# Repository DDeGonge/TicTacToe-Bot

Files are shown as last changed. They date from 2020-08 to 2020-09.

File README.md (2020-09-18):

# TicTacToe-Bot
Its a robot that plays tic tac toe.....

Build at your own risk, documentation is limited and the BOM below is NOT verified.

## BOM
* ~300g filament
* 4x 625 bearings
* 3x low profile gt2 20t 6mm drive pulleys
* 200mm gt2 closed loop belt
* 240mm gt2 closed loop belt
* 11x M3x6 SHCS (*BHCS probably better*) bolt. 4x more for the electronics box lid.
* 5x M3x16 SHCS bolts. Maybe get some M3x18 too just in case :D
* 1x M5x16 SHCS bolt
* 1x M5x40 SHCS bolt
* 2x M5 Nut
* 6x M3 Nut
* A few M3 and M5 washers
* some paper clips to connect servo to pen sleeve
* Uniball 60151 pen, or any other that are a similar size to fit in the sleeve.
* Some M2 bolt and nuts for raspberry pi camera mounting

* 2x nema 17 steppers, <=40mm length
* 1x mg90 servo
* Raspberry pi zero w
* Raspberry pi camera V1.X
* Adafruit Feather M4 or similar
* Stepper drivers, mine go one a custom pcb (files in repo) but you can solder your own or buy an OTS one
* MAX98357 I2S Audio Amplifier Module
* 8 ohm speaker

If you find any errors, please open an issue ticket!

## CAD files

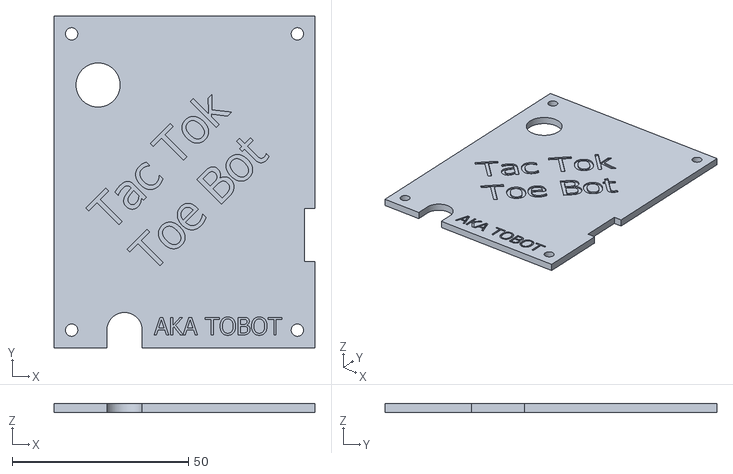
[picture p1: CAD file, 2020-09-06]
cad/Electronics Lid.stl
74.0 x 94.0 x 2.50

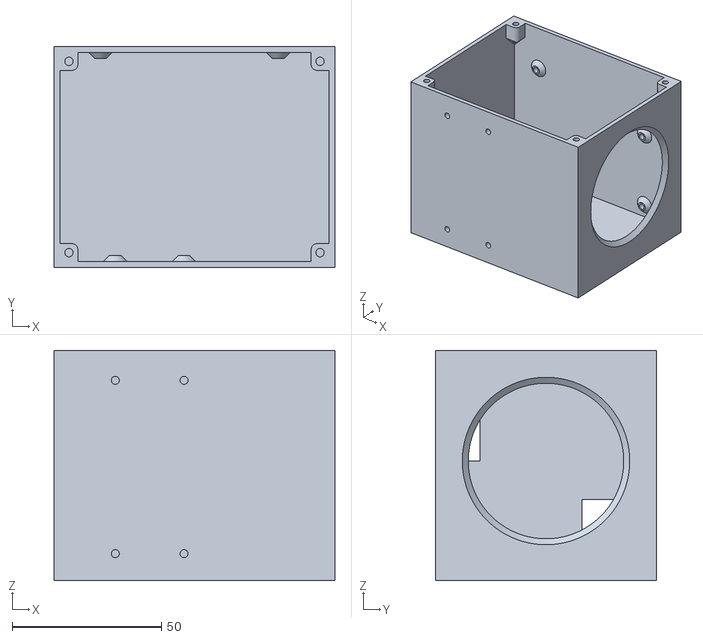
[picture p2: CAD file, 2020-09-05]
cad/Electronics Box.stl
94.0 x 74.0 x 77.0

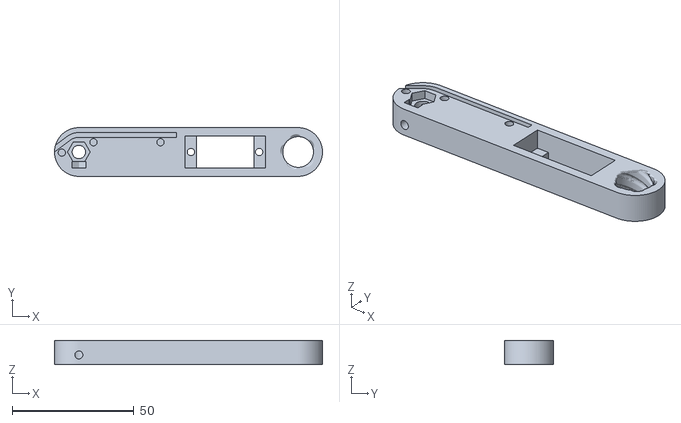
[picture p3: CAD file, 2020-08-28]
cad/Scara2.stl
110.0 x 20.0 x 10.0

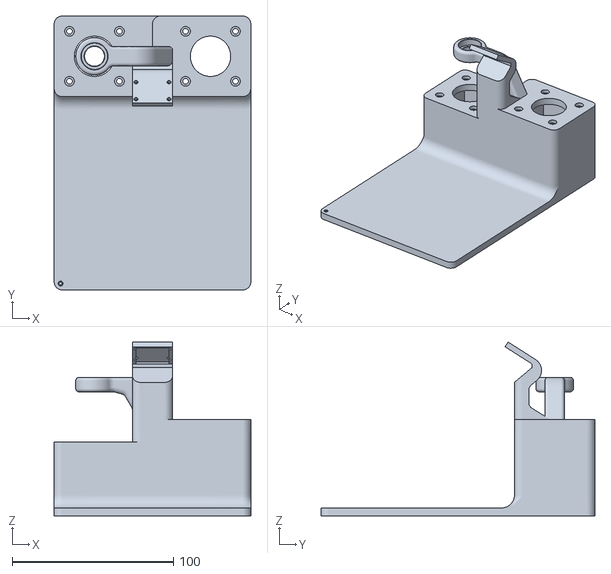
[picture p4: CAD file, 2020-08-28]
cad/Base.stl
122.0 x 170.0 x 107.9

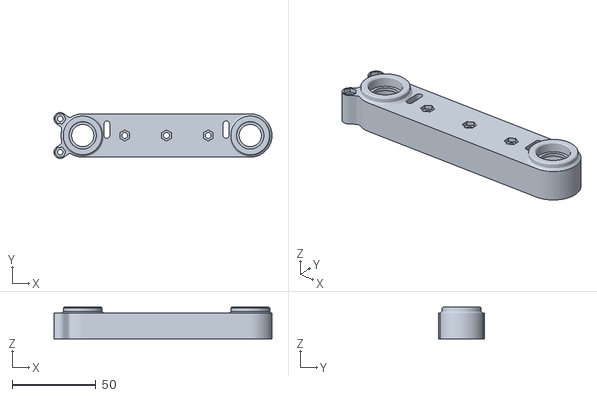
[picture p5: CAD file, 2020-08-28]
cad/Scara1.stl
130.5 x 27.5 x 19.0

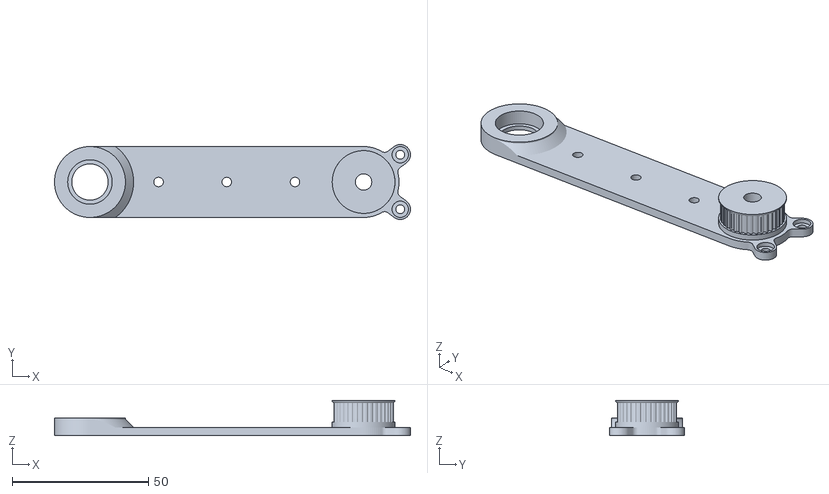
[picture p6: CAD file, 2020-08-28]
cad/Scara1_top.stl
130.5 x 27.5 x 13.0

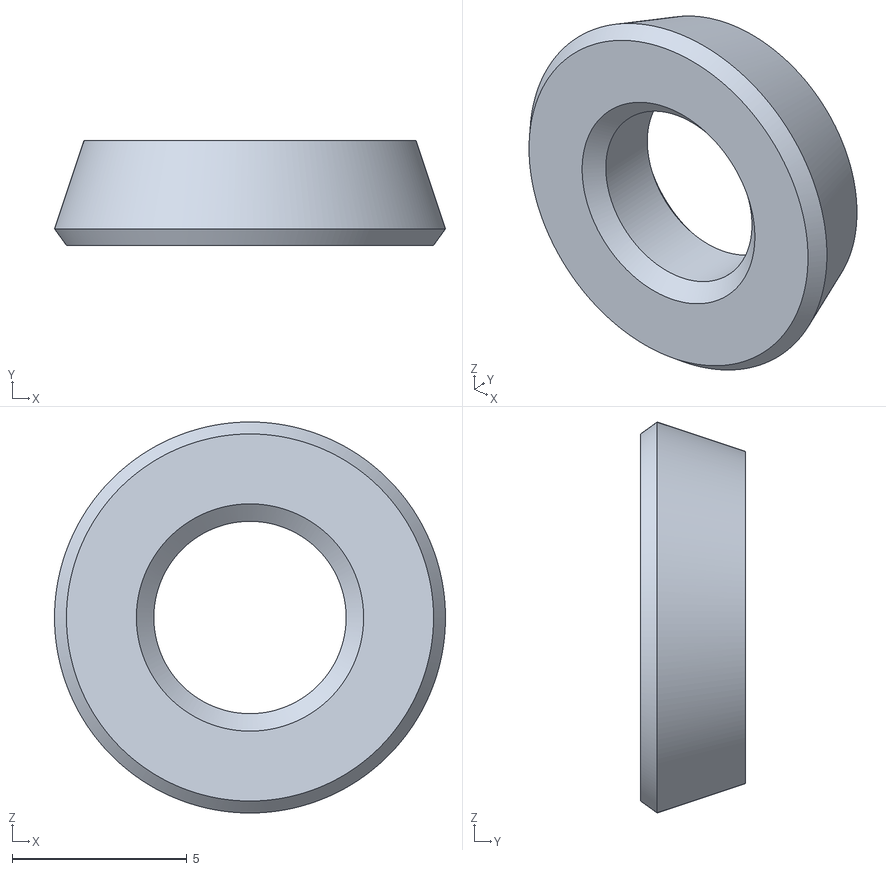
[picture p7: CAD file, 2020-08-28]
cad/PulleySpacer.stl
11.2 x 3.00 x 11.2

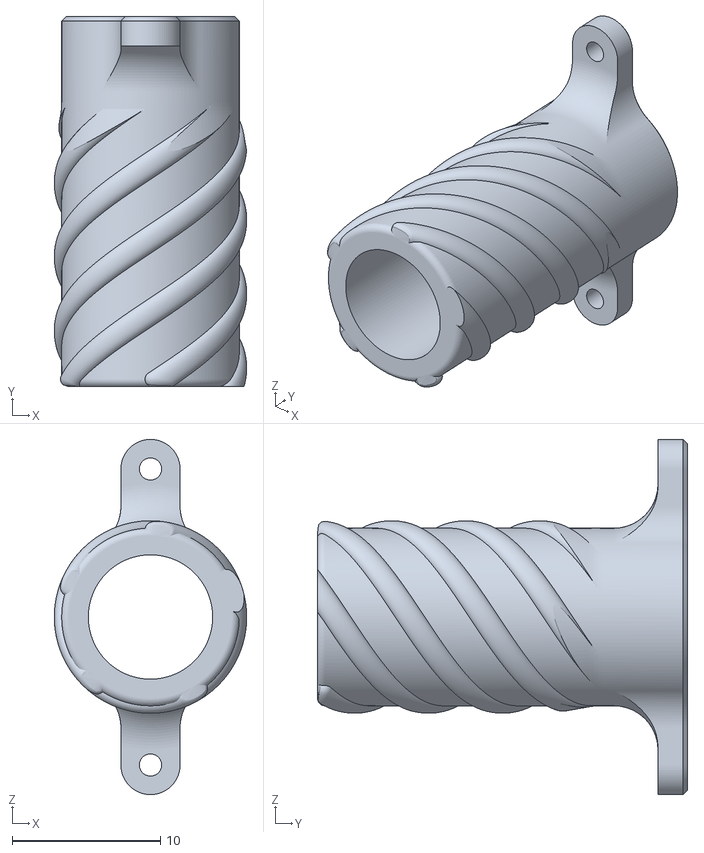
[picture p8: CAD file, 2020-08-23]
cad/Pen Sleeve.stl
13.0 x 25.0 x 24.0

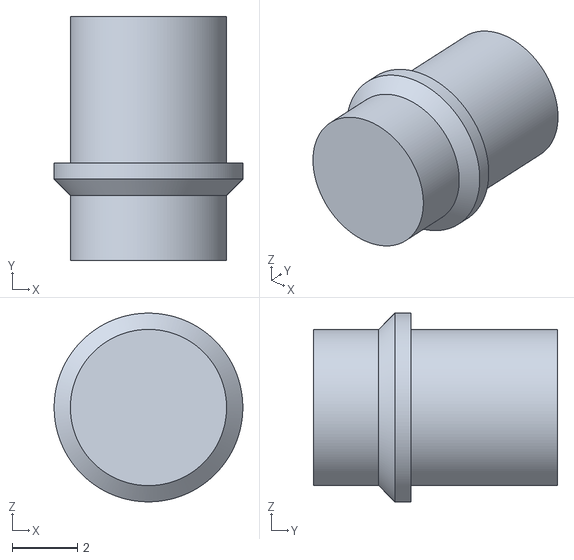
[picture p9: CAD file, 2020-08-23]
cad/Stepper Shaft Extension.stl
5.80 x 7.50 x 5.80

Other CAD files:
cad/625 Bearing.ipt
cad/Base.ipt
cad/Electronics Box.ipt
cad/Electronics Lid.ipt
cad/GT2 20T Drive Pulley.ipt
cad/GT2 Idler Pulley.ipt
cad/MG90servo_body.ipt
cad/Main Assembly.iam
cad/Nema 17.ipt
cad/OldVersions/Base.0059.ipt
cad/OldVersions/Electronics Box.0004.ipt
cad/OldVersions/Main Assembly.0053.iam
cad/OldVersions/Pen Sleeve.0014.ipt
cad/OldVersions/PulleySpacer.0001.ipt
cad/OldVersions/Scara1.0039.ipt
cad/OldVersions/Scara1_top.0033.ipt
cad/OldVersions/Scara2.0021.ipt
cad/OldVersions/Stepper Shaft Extension.0001.ipt
cad/OldVersions/pen.0001.ipt
cad/OldVersions/scara math.0005.ipt
cad/Pen Sleeve.ipt
cad/PulleySpacer.ipt
cad/Scara1.ipt
cad/Scara1_top.ipt
cad/Scara2.ipt
cad/Stepper Shaft Extension.ipt
cad/pen.ipt
cad/scara math.ipt

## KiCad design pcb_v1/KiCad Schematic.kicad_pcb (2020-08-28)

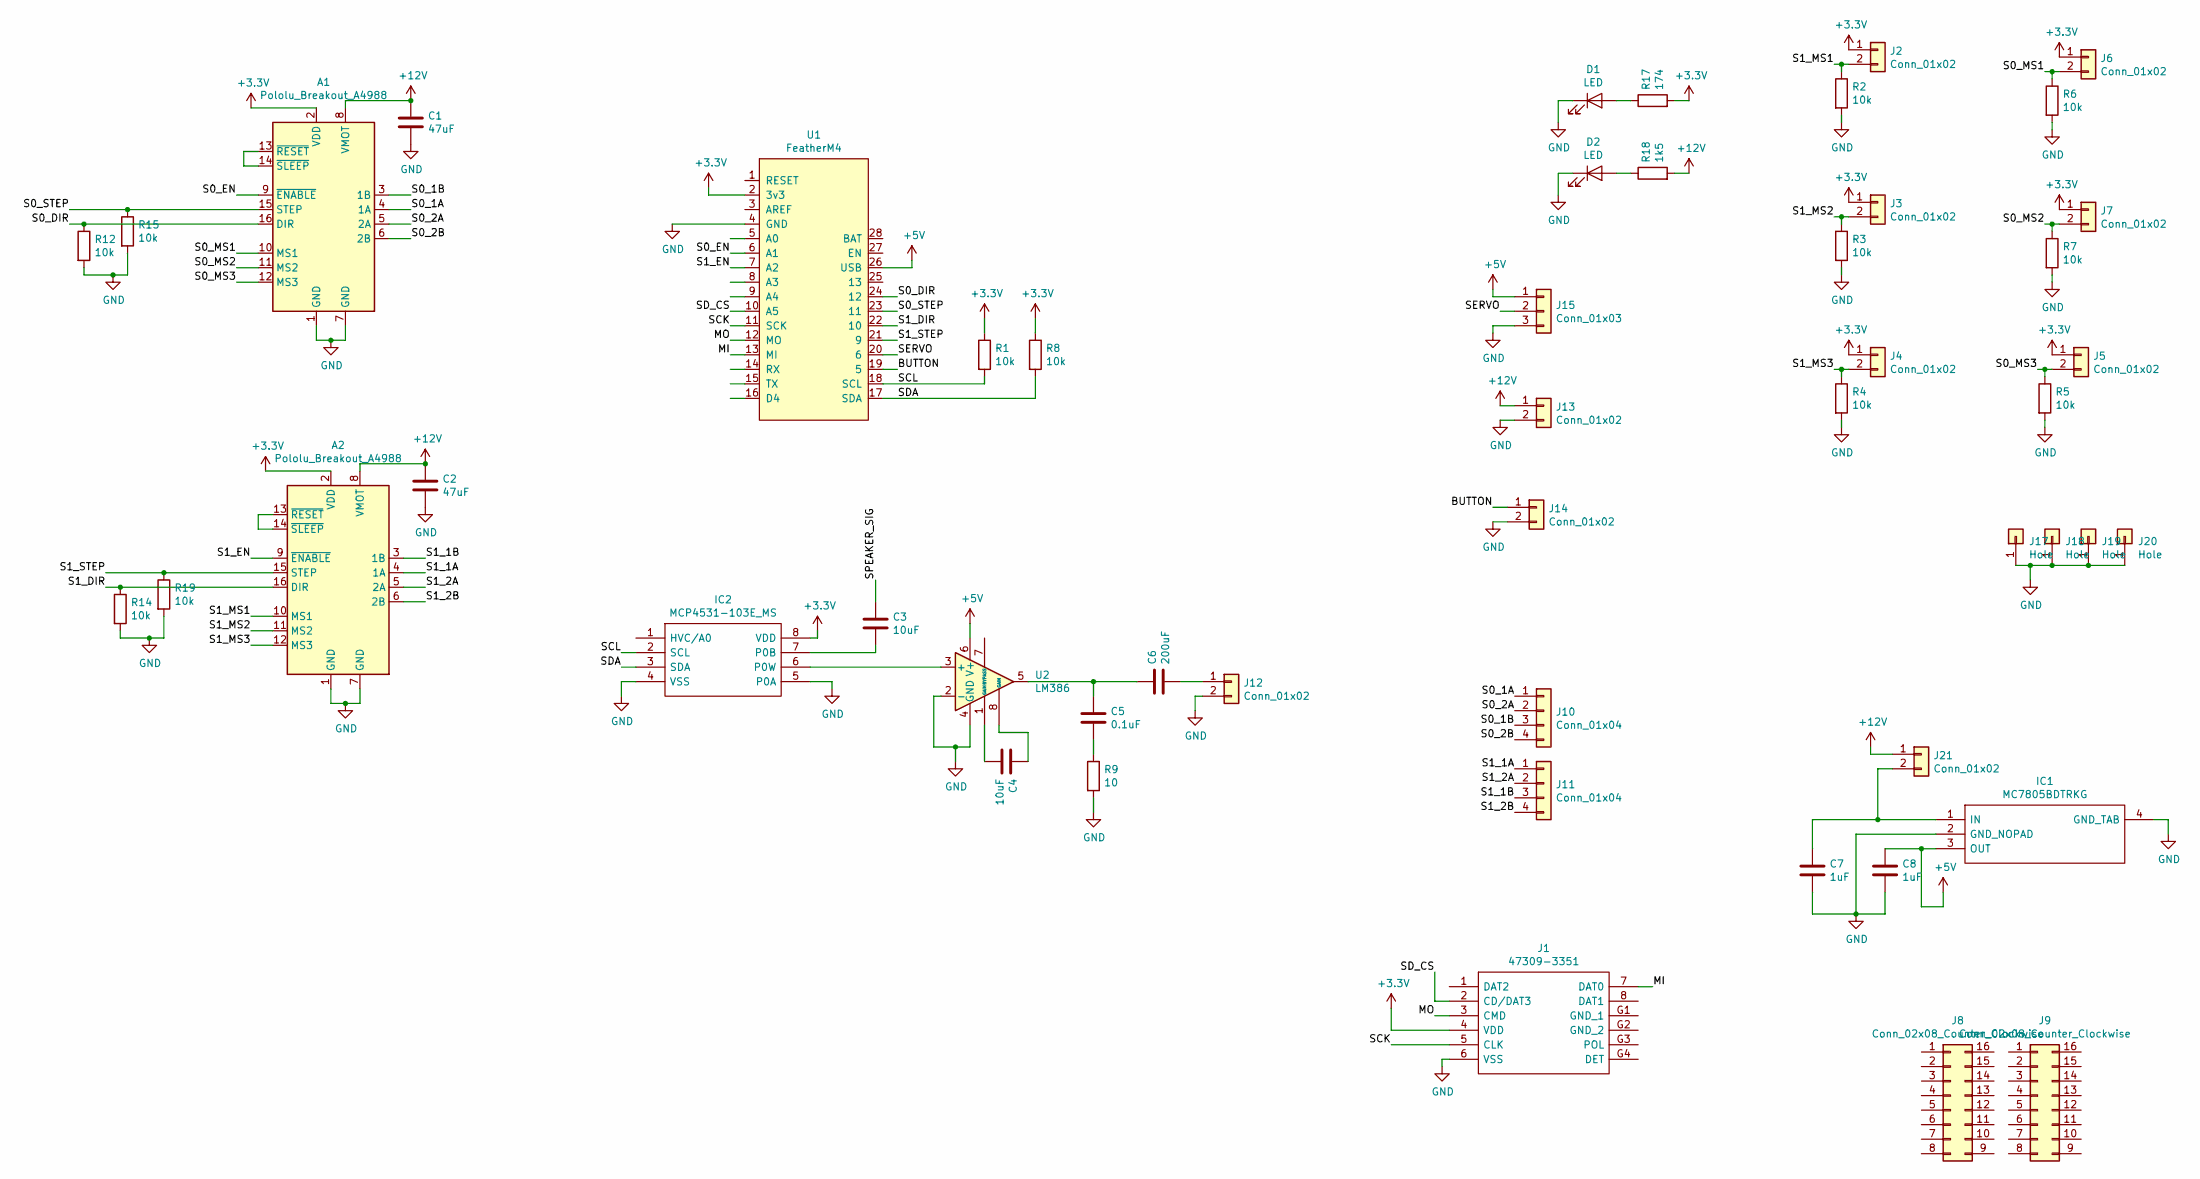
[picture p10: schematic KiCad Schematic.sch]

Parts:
A1, A2: Pololu_Breakout_A4988; Pololu_Breakout-16_15.2x20.3mm
C1, C2: 47uF; CP_Elec_6.3x5.8
C3, C4: 10uF; C_Radial_D5.0mm_H11.0mm_P2.00mm
C5: 0.1uF; C_0402_1005Metric
C6: 200uF; C_Radial_D6.3mm_H7.0mm_P2.50mm
C7, C8: 1uF; C_1206_3216Metric
D1, D2: LED; LED_0603_1608Metric
IC1: MC7805BDTRKG; TO229P990X238-4N; Mouser Part Number 863-MC7805BDTRKG
IC2: MCP4531-103E_MS; SOP65P490X110-8N; Mouser Part Number 579-MCP4531-103E/MS
J1: 47309-3351; 473093351; Mouser Part Number 538-47309-3351
J2, J3, J4, J5, J6, J7, J12, J14, J21: Conn_01x02; PinHeader_1x02_P2.54mm_Vertical
J8, J9: Conn_02x08_Counter_Clockwise; PinHeader_2x08_P2.54mm_Vertical
J10, J11: Conn_01x04; PinSocket_1x04_P2.54mm_Vertical
J13: Conn_01x02; BarrelJack_Wuerth_6941xx301002
J15: Conn_01x03; PinHeader_1x03_P2.54mm_Vertical
J17, J18, J19, J20: Hole; MountingHole_2.7mm_M2.5_DIN965_Pad
R1, R2, R3, R4, R5, R6, R7, R8, R12, R14, R15, R19: 10k; R_0603_1608Metric
R9: 10; R_0603_1608Metric
R17: 174; R_0603_1608Metric
R18: 1k5; R_0603_1608Metric
U1: FeatherM4; FeatherFootprint
U2: LM386; SOIC-8_3.9x4.9mm_P1.27mm

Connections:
+3V3: A1.2 (VDD), A2.2 (VDD), IC2.8 (VDD), J1.4 (VDD), J2.1, J3.1, J4.1, J5.1, J6.1, J7.1, R1.1, R8.1, R17.2, U1.2 (3v3)
+5V: C8.1, IC1.3 (OUT), J15.1, U1.26 (USB), U2.6 (V+)
+12V: A1.8 (VMOT), A2.8 (VMOT), C1.1, C2.1, J13.1, J21.1, R18.2
/BUTTON: J14.1, U1.19 (5)
/MI: J1.7 (DAT0), U1.13 (MI)
/MO: J1.3 (CMD), U1.12 (MO)
/S0_1A: A1.4 (1A), J10.1
/S0_1B: A1.3 (1B), J10.3
/S0_2A: A1.5 (2A), J10.2
/S0_2B: A1.6 (2B), J10.4
/S0_DIR: A1.16 (DIR), R12.1, U1.24 (12)
/S0_EN: A1.9 (~ENABLE), U1.6 (A1)
/S0_MS1: A1.10 (MS1), J6.2, R6.1
/S0_MS2: A1.11 (MS2), J7.2, R7.1
/S0_MS3: A1.12 (MS3), J5.2, R5.1
/S0_STEP: A1.15 (STEP), R15.1, U1.23 (11)
/S1_1A: A2.4 (1A), J11.1
/S1_1B: A2.3 (1B), J11.3
/S1_2A: A2.5 (2A), J11.2
/S1_2B: A2.6 (2B), J11.4
/S1_DIR: A2.16 (DIR), R14.1, U1.22 (10)
/S1_EN: A2.9 (~ENABLE), U1.7 (A2)
/S1_MS1: A2.10 (MS1), J2.2, R2.1
/S1_MS2: A2.11 (MS2), J3.2, R3.1
/S1_MS3: A2.12 (MS3), J4.2, R4.1
/S1_STEP: A2.15 (STEP), R19.1, U1.21 (9)
/SCK: J1.5 (CLK), U1.11 (SCK)
/SCL: IC2.2 (SCL), R1.2, U1.18 (SCL)
/SDA: IC2.3 (SDA), R8.2, U1.17 (SDA)
/SD_CS: J1.2 (CD/DAT3), U1.10 (A5)
/SERVO: J15.2, U1.20 (6)
/SPEAKER_SIG: C3.1
GND: A1.1 (GND), A1.7 (GND), A2.1 (GND), A2.7 (GND), C1.2, C2.2, C7.2, C8.2, D1.1 (K), D2.1 (K), IC1.2 (GND_NOPAD), IC1.4 (GND_TAB), IC2.4 (VSS), IC2.5 (P0A), J1.6 (VSS), J12.2, J13.2, J14.2, J15.3, J17.1, J18.1, J19.1, J20.1, R2.2, R3.2, R4.2, R5.2, R6.2, R7.2, R9.2, R12.2, R14.2, R15.2, R19.2, U1.4 (GND), U2.2 (-), U2.4 (GND)
unnamed: A1.13 (~RESET), A1.14 (~SLEEP)
unnamed: A2.13 (~RESET), A2.14 (~SLEEP)
unnamed: C3.2, IC2.7 (P0B)
unnamed: C4.1, U2.8 (GAIN)
unnamed: C4.2, U2.1 (GAIN)
unnamed: C5.1, C6.1, U2.5
unnamed: C5.2, R9.1
unnamed: C6.2, J12.1
unnamed: C7.1, IC1.1 (IN), J21.2
unnamed: D1.2 (A), R17.1
unnamed: D2.2 (A), R18.1
unnamed: IC2.6 (P0W), U2.3 (+)

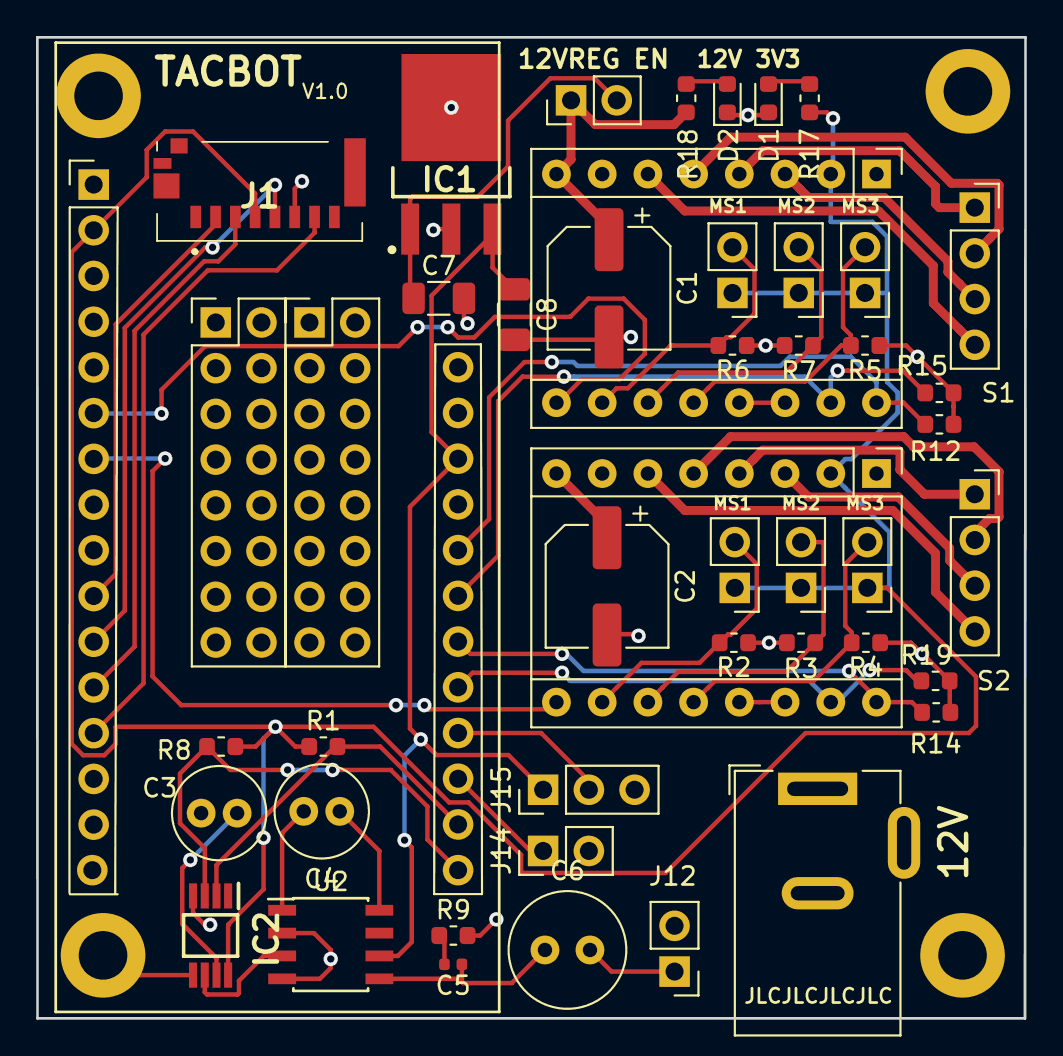
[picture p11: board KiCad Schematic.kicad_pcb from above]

Board: 2 copper layers, 54.9 x 54.5 mm, 51 parts (0 on the bottom side), 44 nets.

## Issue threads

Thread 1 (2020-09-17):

A couple clarifications

kmatch98, 2020-09-17:

kmatch98, 2020-09-17:
First, this is awesome!  End of last year I made a two link robot arm and wanted to make a GCode plotter but I couldn’t stomach to do the math and so I just let it lie dormant. Thanks for doing this!

I have a couple of questions for you:
1.  What does this x and y offset mean?  Maybe a napkin drawing would help?
```
float x0_offset_mm = 25;
 float y0_offset_mm = 135;
```

2.  I see that the homing routine isn’t written, but how do you manage it anyway? Maybe related to above, If my homing position is different would the homing position affect the offsets?

3.  The arc drawing is missing. Do you have a way of generating gcode with only lines?

Thanks a lot for this, and thanks for sharing.

DDeGonge, 2020-09-17:
Sorry I'm pretty terrible at documenting things, I intend to at least improve the readme by the weekend!

1. These are the distances from the 0,0 position to the point of rotation where the first arm connects to the base. Basically where the scara arm starts.

2. I do have a janky "homing" routine function which simply allows you to move the bot so the pen is near zero, it then enables the motor and lets you fine tune the position before accepting. It isn't great but I didn't add any limit switches to the hardware so this was the best I could do haha.

3. I just use Cura and added custom retraction code for my pen. It seems to not use any arcs in the gcode it produces but your results may vary. You could always take a crack at implementing arc control, I'd be happy to merge it into my code if you are successful :D

Closed 2020-09-18.

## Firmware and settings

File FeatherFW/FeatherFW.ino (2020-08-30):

#include "tacbot.h"
#include "funks.h"

#define Serial SERIAL_PORT_USBVIRTUAL

// Speaker stuff
//Adafruit_VS1053_FilePlayer musicPlayer = 
//  Adafruit_VS1053_FilePlayer(VS1053_RESET, VS1053_CS, VS1053_DCS, VS1053_DREQ, CARDCS);

void setup()
{
  // Init serial, sd, musicplayer, and neopixel
  Serial.begin(250000);
  while (!Serial) { delay(1); }
  pixel.begin();
//  if (! musicPlayer.begin()) { // initialise the music player
//     Serial.println(F("Couldn't find VS1053, do you have the right pins defined?"));
//     error_blink(2);
//  }
//  Serial.println(F("VS1053 found"));
//
//  if (!SD.begin(CARDCS)) {
//    Serial.println("SD initialization failed.");
//    error_blink(3);
//  } else {
//    Serial.println("SD initialization successful.");
//  }

  // Configure music player
//  musicPlayer.setVolume(1,1);  // Lower values is louder. I only use right channel
//  musicPlayer.useInterrupt(VS1053_FILEPLAYER_PIN_INT);
}

void loop()
{
  // Initialize some stuff
  setLEDColor(200, 0, 0);
  unsigned long startTime_us = micros();
  unsigned long t_elapsed_us;
  Servo pen_servo;
  pen_servo.attach(servo_pin);
  stepper s0, s1;
  s0.init(s0_step, s0_dir, s0_en, false);
  s1.init(s1_step, s1_dir, s1_en, false);

  scara_bot bot;
  bot.init(s0, s1, pen_servo);

  char serial_data[MAX_MSG_LEN];
  setLEDColor(100, 0, 0);

  // Init vars
  char base_cmd, char_value;
  int32_t base_value, int_value;
  float float_value;

  // Start main response loop
  while (true)
  {
    t_elapsed_us = micros() - startTime_us;
    clear_data(serial_data);
    if (respondToSerial(serial_data)) 
    {
      setLEDColor(100, 50, 0);

      // Parse input into data chunks
      vector<string> args;
      parse_inputs(serial_data, args);
      parse_int(args[0], base_cmd, base_value);

      switch (tolower(base_cmd)) 
      {
        case 'g': {
          switch (base_value) 
          {
            case 0:
            case 1: {
              // LINEAR MOVE
              float xpos, ypos, feedrate;
              gcode_command_floats gcode(args);
              bot.move_motor_linear(gcode.fetch('x'), gcode.fetch('y'), gcode.fetch('f'));
              break;
            }
            case 2: {
              // ARC MOVE CW
              gcode_command_floats gcode(args);
              bot.move_motor_arc(gcode.fetch('x'), gcode.fetch('y'), gcode.fetch('i'), gcode.fetch('j'), gcode.fetch('f'), true);
              break;
            }
            case 3: {
              // ARC MOVE CCW
              gcode_command_floats gcode(args);
              bot.move_motor_arc(gcode.fetch('x'), gcode.fetch('y'), gcode.fetch('i'), gcode.fetch('j'), gcode.fetch('f'), false);
              break;
            }
            case 28: {
              Serial.println("TODO homing");
              break;
            }
            case 90: {
              // Absolute positioning
              bot.set_pos_mode(true);
              break;
            }
            case 91: {
              // Relative positioning
              bot.set_pos_mode(false);
              break;
            }
            case 92: {
              // This is implemented wrong currently but idc deal with it
              gcode_command_floats gcode(args);
              bot.zero(gcode.fetch('x'), gcode.fetch('y'));
              break;
            }
          }
          break;
        }
      case 'm': {
          switch (base_value) 
          {
            case 17: {
              // Enable Steppers
              gcode_command_floats gcode(args);
              bot.enable_motors(gcode.com_exists('x'), gcode.com_exists('y'));
              break;
            }
            case 84: {
              // Disable Steppers
              gcode_command_floats gcode(args);
              bot.disable_motors(gcode.com_exists('x'), gcode.com_exists('y'));
              break;
            }
            case 114: {
              // Get current position
              float xpos, ypos;
              bot.get_pos(xpos, ypos);
              Serial.println("TODO FINISH THIS ONE");
              break;
            }
            case 201: {
              // Set Acceleration Limits
              gcode_command_floats gcode(args);
              bot.set_def_speeds(gcode.fetch('a'), gcode.fetch('v'));
              break;
            }
          }
          break;
        }
      case 'c': {
          switch (base_value) 
          {
            case 0: {
              // configure hardware stuff
              gcode_command_floats gcode(args);
              bot.configure(gcode.fetch('a'), gcode.fetch('b'), gcode.fetch('c'), gcode.fetch('d'), gcode.fetch('e'), gcode.fetch('f'), gcode.fetch('g'), gcode.fetch('h'));
              break;
            }
            case 1: {
              // Lower pen servo
              bot.lower_pen();
              break;
            }
            case 2: {
              // Raise pen servo
              bot.raise_pen();
              break;
            }
            case 3: {
              // Play a tune!
              string str = "/" + args[1] + ".mp3";
              const char* strdata = str.data();
//              musicPlayer.playFullFile(strdata);
              break;
            }
          }
        }
        break;
      }
      Serial.println("ok");
      setLEDColor(0, 100, 0);
    }
  }
}

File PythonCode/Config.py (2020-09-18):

""" DEBUG PARAMS """
DEBUG_MODE = False


""" MECHANICAL PARAMETERS """
s0_step_per_rev = 5760
s1_step_per_rev = 3200

# default_vel_mmps = 800.0
# default_accel_mmps2 = 40000.0
default_vel_mmps = 250.0
default_accel_mmps2 = 10000.0

s0_arm_len_mm = 100.5
s1_arm_len_mm = 90.0

pen_up_pwm = 100
pen_dn_pwm = 70

x_zero_offset = 21
y_zero_offset = 141

board_center_x_mm = 60
board_center_y_mm = 50
box_size_mm = 20


""" OPERATION PARAMETERS """
gcode_folder = 'gcode'
audio_path = 'audio'


""" CAMERA PARAMETERS """
# Cropped region corner points, consider rotation plz
p0 = [145, 115] # TL
p1 = [520, 100] # TR
p2 = [175, 400] # BL
p3 = [470, 385] # BR

IMAGE_RESOLUTION = (648,486)
IMAGE_ROTATION_DEGS = 0

POST_TRANSFORM_RES = [400,400]

TAC_BOX_CENTERS = [
    (67, 67),
    (67, 200),
    (67, 333),
    (200, 67),
    (200, 200),
    (200, 333),
    (333, 67),
    (333, 200),
    (333, 333)
]

TAC_BOX_X = 90
TAC_BOX_Y = 90


""" OPENCV PARAMETERS """
MOTION_MIN_CHANGE = 1.0


""" SPEAKER PARAMETERS """
freq = 44100    # audio CD quality
bitsize = -16   # unsigned 16 bit
channels = 2    # 1 is mono, 2 is stereo
buffer = 2048   # number of samples (experiment to get right sound)
volume = 0.95


""" FEATHER COMM PARAMETERS """
# Chars used for setting parameters on feather. All vars here must be int
Feather_Parameter_Chars = {
    'a': s0_arm_len_mm,
    'b': s1_arm_len_mm,
    'c': s0_step_per_rev,
    'd': s1_step_per_rev,
    'e': x_zero_offset,
    'f': y_zero_offset,
    'g': pen_up_pwm,
    'h': pen_dn_pwm
}

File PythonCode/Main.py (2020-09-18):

__version__ = '0.1.0'

import time
import Config as cfg
import random
from SerialDevice import *
from ScaraDriver import *
from CameraDriver import *
from SpeakerDriver import *
from OtherStuff import *
from Gameplay import *


def main():
    try:
        serdev = SerialDevice()
        scarabot = Scara(serdev)
        cam = Camera()
        spkr = Speaker()

        scarabot.user_zero()
        scarabot.park()
        cam.start_camera()

        while True:
            inpt = input('Press enter to start game...')

            # Future improvements can happen here
            bot_first = True  # random.choice([True, False])
            game_function = 'standard'  # random.choice(GAMETYPES)

            if inpt == 'c':
                spkr.set_cat_mode()
            else:
                spkr.set_human_mode()

            # Start game
            if game_function == 'standard':
                standard_game(scarabot, cam, spkr, bot_first = bot_first)
            elif game_function == 'meme':
                meme_game(scarabot, cam, spkr, bot_first = bot_first)

            scarabot.park()
                
    except Exception as e:
        raise e


if __name__=='__main__':
    # main()

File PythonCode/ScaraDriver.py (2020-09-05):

__version__ = '0.1.0'

import Config as cfg
import os
import time
import math

class Scara(object):
    def __init__(self, serial_device):
        self.serial_device = serial_device
        self.x_error = 0.
        self.y_error = 0.
        self.configure()
        self.update_defaults()
        self.is_parked = False

    """ Motion stuff """

    def configure(self):
        command_string = 'C0'
        for k, v in cfg.Feather_Parameter_Chars.items():
            command_string += ' {}{}'.format(k, v)
        self.serial_device.command(command_string)

    def home(self):
        print('TODO implement this plz')

    def zero(self):
        self.serial_device.command('G92 X0 Y0')

    def enable(self):
        self.serial_device.command('M17')

    def disable(self):
        self.serial_device.command('M84')

    def user_zero(self):
        # Too lazy to implement limit switches so now I have to do this..
        self.disable()
        self.lower_pen()
        _ = input('Press enter when near zero...')
        self.enable()
        while True:
            com = input('Enter commands to move closer to zero in format "x,y", units are mm. Or press enter to continue: ')
            if com == '':
                break
            else:
                com = com.split(',')
                if len(com) == 2:
                    self.zero()
                    self.absolute_move(float(com[0]), float(com[1]))

        self.zero()
        self.raise_pen()

    def park(self):
        if self.is_parked is False:
            self.serial_device.command('G1 X-30 Y90')
            self.serial_device.command('G1 Y130')
        self.is_parked = True

    def unpark(self):
        if self.is_parked is True:
            self.serial_device.command('G1 X-30 Y90')
            self.serial_device.command('G1 X0 Y0')
        self.is_parked = False

    def raise_pen(self):
        self.serial_device.command('C2')

    def lower_pen(self):
        self.serial_device.command('C1')

    def update_defaults(self, vel = None, acc = None):
        if acc == None:
            acc = cfg.default_accel_mmps2
        if vel == None:
            vel = cfg.default_vel_mmps
        self.serial_device.command('M201 a{} v{}'.format(acc, vel))

    def absolute_move(self, xtar_mm, ytar_mm, velocity_mmps=None):
        # Calculate move
        command = 'G0 X{} Y{}'.format(xtar_mm, ytar_mm)
        if velocity_mmps is not None:
            command += ' F{}'.format(velocity_mmps * 60)
        self.serial_device.command(command)

    def relative_move(self, xtar_mm, ytar_mm, velocity_mmps=None):
        return self.absolute_move(xpos_mm + xtar_mm, ypos_mm + ytar_mm, velocity_mmps)

    def draw_move(self, move):
        x_center = cfg.board_center_x_mm + (move.x - 1) * cfg.box_size_mm
        y_center = cfg.board_center_y_mm + (1 - move.y) * cfg.box_size_mm
        self.absolute_move(x_center, y_center)
        self.send_gcode('draw_x.g')

    def draw_board(self):
        self.send_gcode('board.g')

    def draw_win_line(self, game):
        if game is None:
            return

        p_start, p_end = game.get_winner_coords()
        p_start_x = cfg.board_center_x_mm + (p_start[0] - 1) * cfg.box_size_mm
        p_start_y = cfg.board_center_y_mm + (1 - p_start[1]) * cfg.box_size_mm
        p_end_x = cfg.board_center_x_mm + (p_end[0] - 1) * cfg.box_size_mm
        p_end_y = cfg.board_center_y_mm + (1 - p_end[1]) * cfg.box_size_mm
        self.absolute_move(p_start_x, p_start_y)
        self.lower_pen()
        self.absolute_move(p_end_x, p_end_y, 100)
        self.raise_pen()

    def send_gcode(self, filename):
        with open(os.path.join(cfg.gcode_folder, filename)) as f:
            while(True):
                line = f.readline().strip('\n')
                if not line:
                    break
                
                if line[0] == ';':
                    # Comments start with semicolon
                    continue

                self.serial_device.command(line)

    @property
    def is_homed(self):
        return True

    @property
    def xpos_mm(self):
        return

    @property
    def ypos_mm(self):
        return

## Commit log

2020-08-23 update cam driver and test script
2020-08-23 bugfixes, finish initial game loop, stuff
    [CameraDriver.py, Config.py, Gameplay.py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]
2020-08-23 many updates and fixes
    [CameraDriver.py, Config.py, Gameplay.py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]
2020-08-24 cad updates, feather fw improvements
    [Base.0044.ipt, Base.0045.ipt, Base.ipt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]
2020-08-28 cad updates for accuracy, add audio support to firmware, config updates
    [Base.0045.ipt, Base.0054.ipt, Base.ipt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]
2020-08-30 cad improvements, firmware bugfixes, more python stuff. Gimme a break I cant keep track of all this
    [Base.0054.ipt, Base.0059.ipt, Base.ipt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]
2020-09-01 add butterfly for fun
    [butter.g]
2020-09-01 bugfixes and maybe fix axis issue with AI
    [butter.g]
2020-09-02 fixing stuff and add swatting
    [CameraDriver.py, Config.py, Gameplay.py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]
2020-09-05 add audio and audio driver, minor cad tweaks
    [Main Assembly.0052.iam, Main Assembly.0053.iam, Main Assembly.iam]
2020-09-05 add ebox cad and integrate speaker into routine
    [Electronics Box.0003.ipt, Electronics Box.ipt, Electronics Box.stl]
2020-09-05 bugfixes for the swatting
    [Config.py, OtherStuff.py]
2020-09-05 draw slower, add park at end of game
    [board.g, draw_x.g]
2020-09-06 add electronics box cad and park optimizationz
    [Electronics Box.0003.ipt, Electronics Box.0004.ipt, Electronics Box.ipt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]
2020-09-13 stuff for memes
    [scara math.0004.ipt, scara math.0005.ipt, scara math.ipt]
